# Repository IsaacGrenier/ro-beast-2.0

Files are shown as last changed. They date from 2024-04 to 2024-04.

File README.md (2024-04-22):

# Ro-Beast 2.0
Repository providing all files needed for the operation and modification of Ro-Beast 2.0, designed and built by Vardaan Malhotra, Isaac Grenier, Ben Lee, and Vince d'Entremont, also known as the Ro-Beast Battle Busters.  
  
Repository includes:
- User manual
- Altium: all schematic and PCB files for the control board
- GUI: Python files for running the GUI
- uC: all files currently programmed on the microcontroller

Software Issues to be Resolved for Full Functionality (as of 2024-04-11)
- [ ] Currently, there is a potential UART overflow issue only allowing one command to be sent to the system. For example, once positioning or a sweep is performed, the system must be turned off and back on to perform another.
- [ ] The real-time values are not being sent to the GUI. The architecture has been built out in the software, but some bugs are hindering this functionality.
- [ ] The status is not being sent to the GUI.
- [ ] The play/pause button functionality must be created.
- [ ] More warnings and errors could be created to ensure the safety and proper operation of the system.

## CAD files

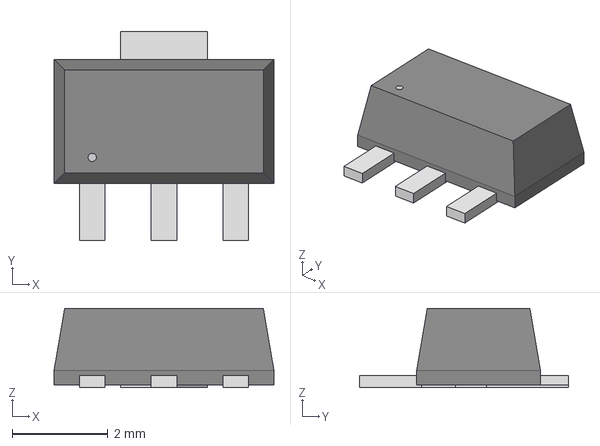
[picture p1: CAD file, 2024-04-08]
Altium/RoBeast_Control_Board/3D Bodies/SOT89_B8D_DIO.step
4.60 x 4.37 x 1.65 mm

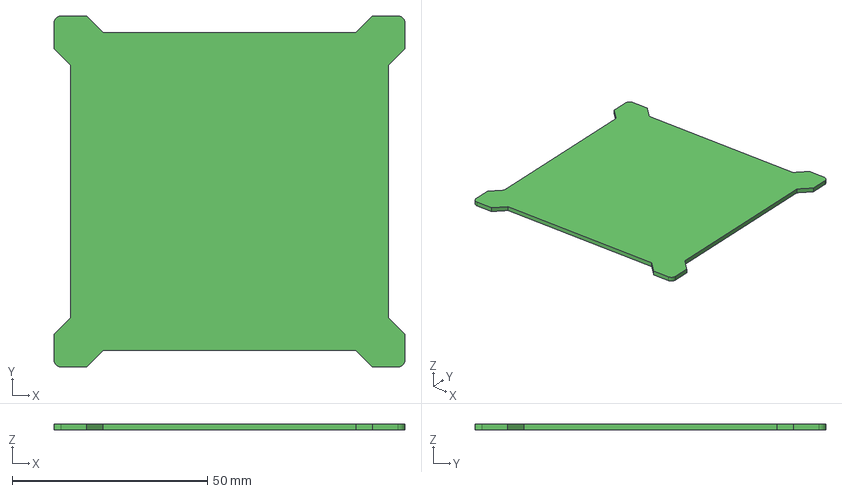
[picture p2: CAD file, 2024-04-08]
Altium/RoBeast_Control_Board/RoBeast_Control_Board_shape.step
89.9 x 89.9 x 1.58 mm

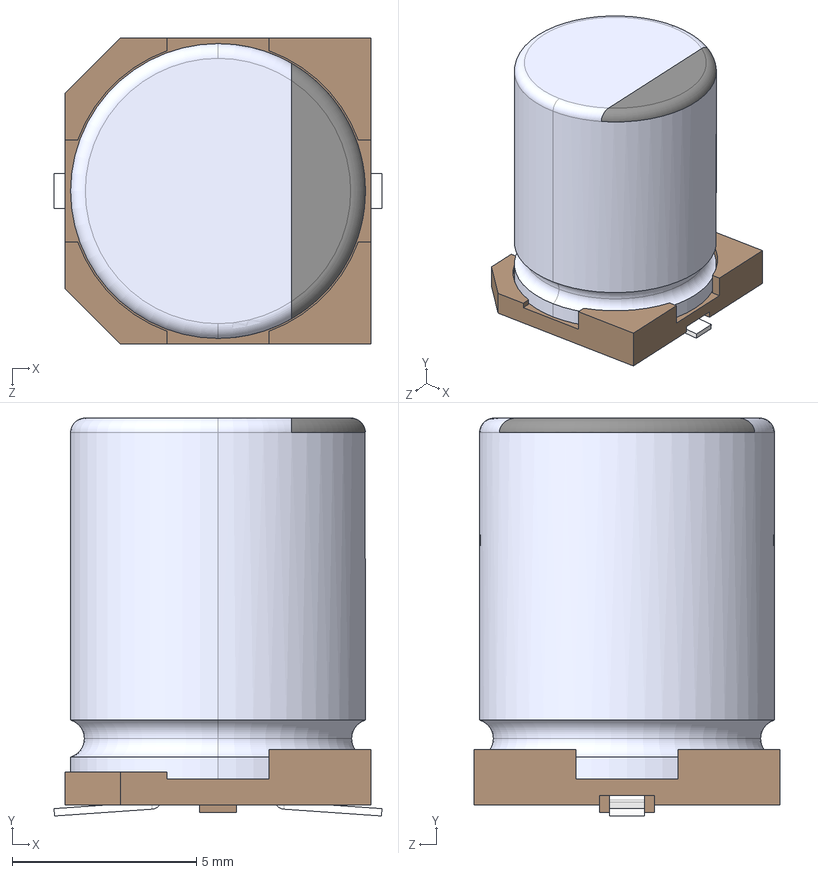
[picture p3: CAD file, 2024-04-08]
Altium/RoBeast_Control_Board/3D Bodies/UCL1V151MNL1GS.step
8.90 x 10.8 x 8.30 mm

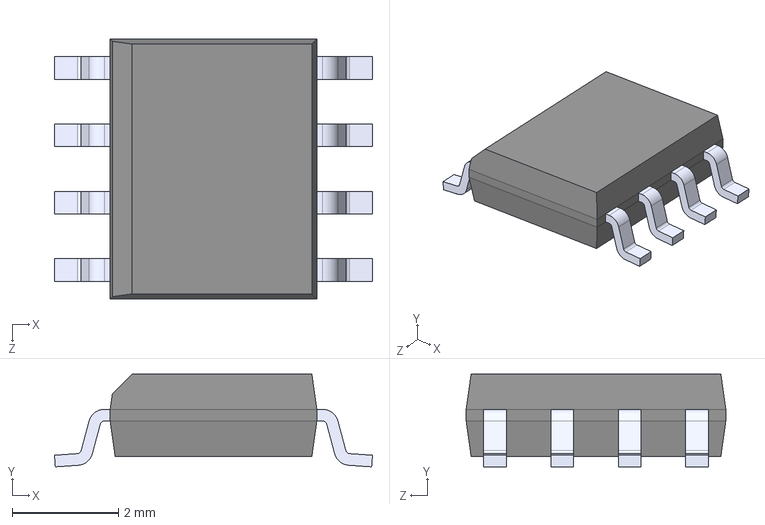
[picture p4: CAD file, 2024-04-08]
Altium/RoBeast_Control_Board/3D Bodies/DG9431EDY-T1-GE3.STEP
6.00 x 1.75 x 4.90 mm

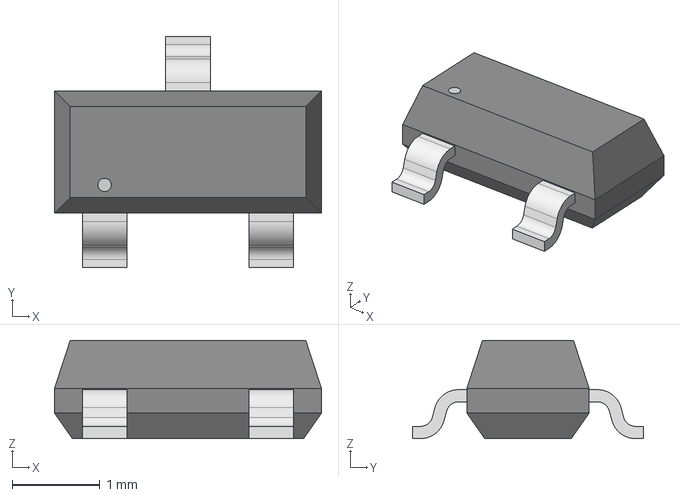
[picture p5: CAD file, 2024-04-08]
Altium/RoBeast_Control_Board/3D Bodies/SOT-23_ONS.step
3.05 x 2.64 x 1.12 mm

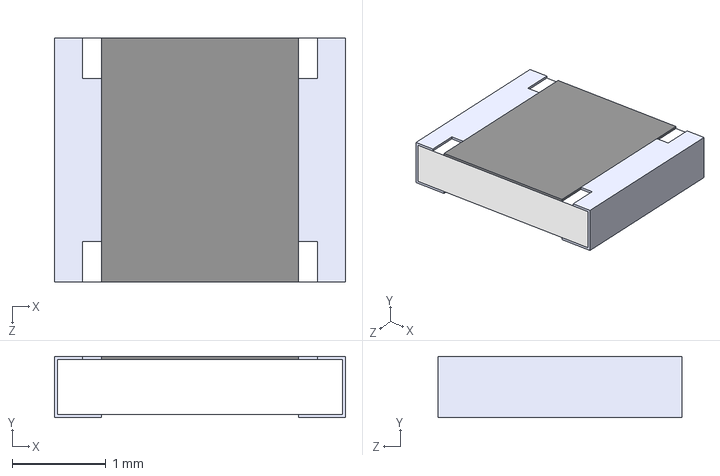
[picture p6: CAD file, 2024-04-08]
Altium/RoBeast_Control_Board/3D Bodies/RC1210JR-070RL.step
3.10 x 0.65 x 2.60 mm

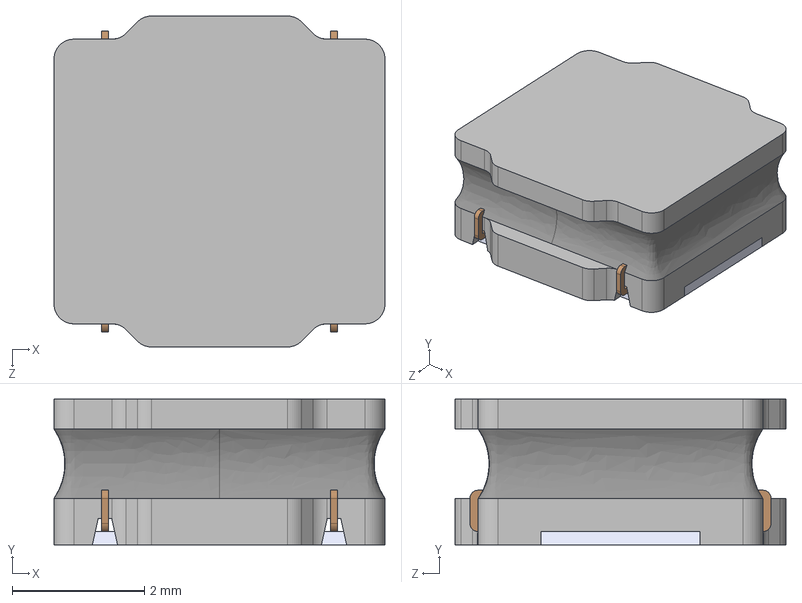
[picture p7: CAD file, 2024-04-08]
Altium/RoBeast_Control_Board/3D Bodies/LQH5BPB1R0NT0L.STEP
5.00 x 2.20 x 5.00 mm

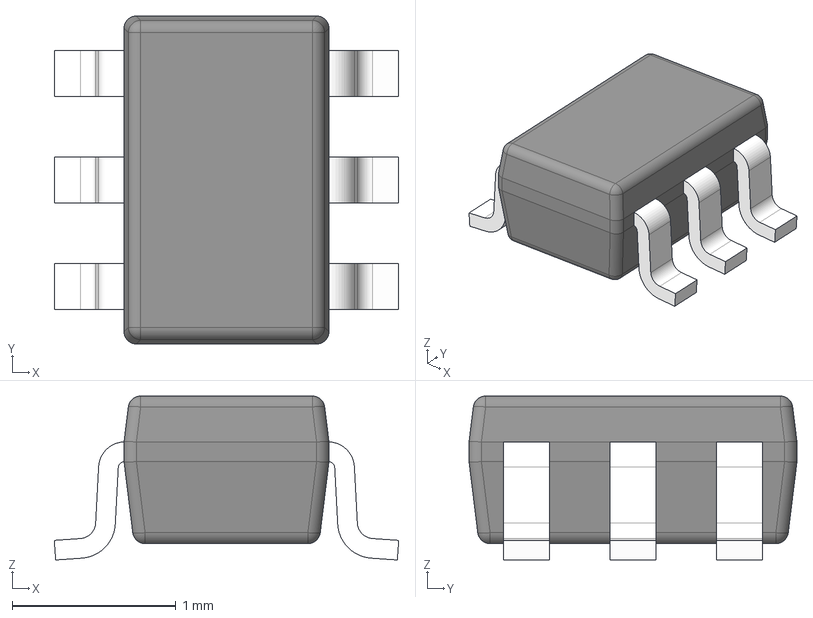
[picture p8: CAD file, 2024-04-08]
Altium/RoBeast_Control_Board/3D Bodies/DCK0006A.stp
2.10 x 2.00 x 1.00 mm
BODY-SOT
LEAD-SOT x 6
PIN1-ID

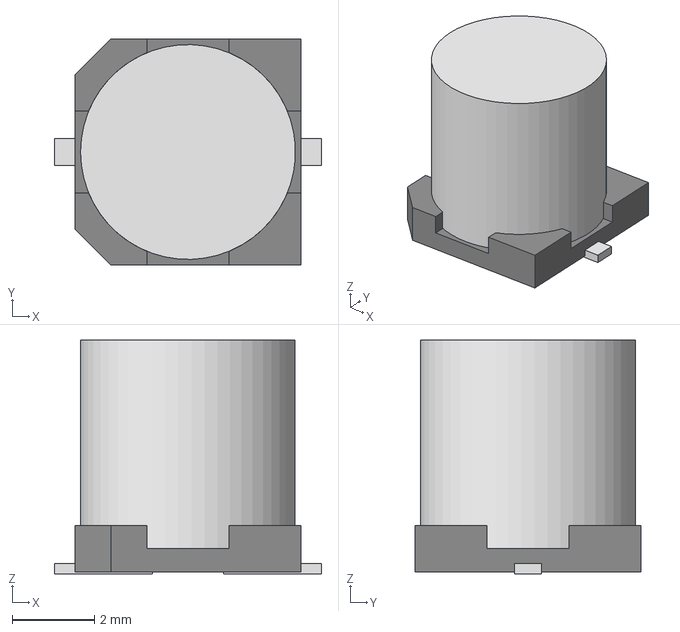
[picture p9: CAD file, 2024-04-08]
Altium/RoBeast_Control_Board/3D Bodies/EXV-9D_KEM.step
6.50 x 5.51 x 5.69 mm

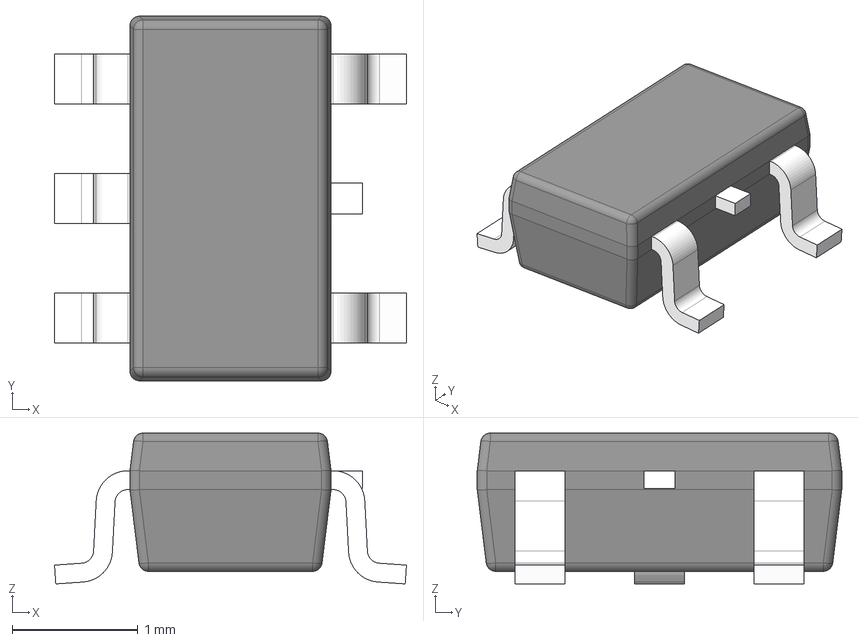
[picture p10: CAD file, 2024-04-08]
Altium/RoBeast_Control_Board/3D Bodies/DBV0005A.stp
2.80 x 2.90 x 1.20 mm
BODY-SOT
LEAD-SOT x 5
LEAD-DUMMY

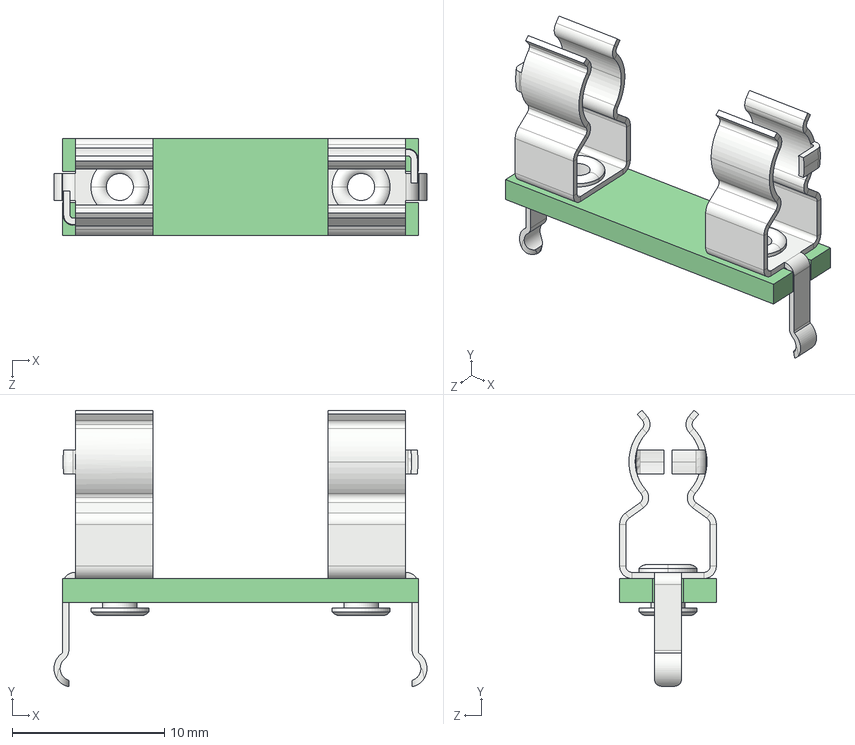
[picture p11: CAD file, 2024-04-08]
Altium/RoBeast_Control_Board/3D Bodies/3527.step
24.5 x 18.2 x 6.35 mm

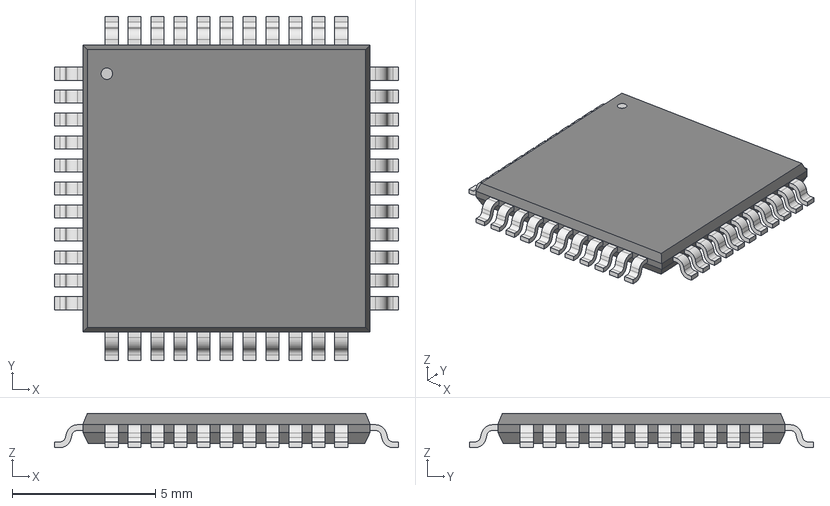
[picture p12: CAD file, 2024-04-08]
Altium/RoBeast_Control_Board/3D Bodies/TQFP44_10x10MC_MCH.step
12.0 x 12.0 x 1.20 mm

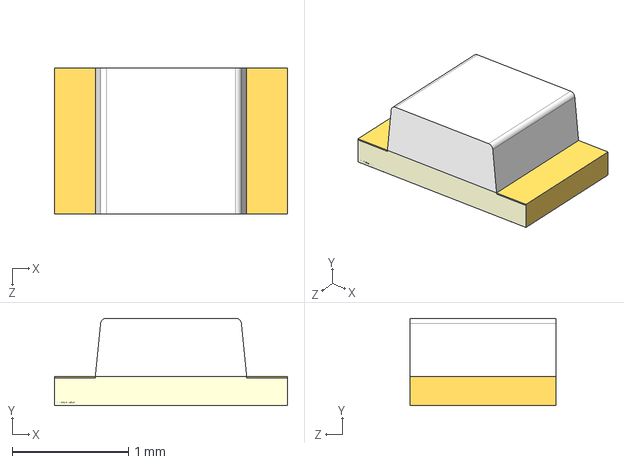
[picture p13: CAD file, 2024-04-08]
Altium/RoBeast_Control_Board/3D Bodies/APT2012.STEP
2.00 x 0.75 x 1.25 mm

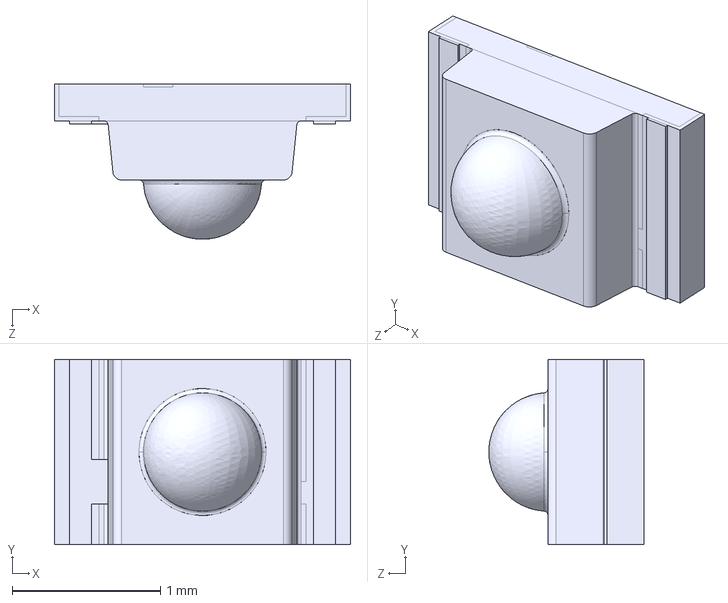
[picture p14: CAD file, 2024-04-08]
Altium/RoBeast_Control_Board/3D Bodies/APTD2012.IGS
2.00 x 1.25 x 1.05 mm

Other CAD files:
Altium/RoBeast_Control_Board/3D Bodies/DCK0005A.stp
Altium/RoBeast_Control_Board/3D Bodies/PH1RA-03-UA.STEP
Altium/RoBeast_Control_Board/3D Bodies/54-00128.STEP
Altium/RoBeast_Control_Board/3D Bodies/IPD50P04P4L-11--3DModel-STEP-56544.STEP
Altium/RoBeast_Control_Board/3D Bodies/015246043.stp
Altium/RoBeast_Control_Board/3D Bodies/0217005.MXP.STEP
Altium/RoBeast_Control_Board/3D Bodies/026013114.stp
Altium/RoBeast_Control_Board/3D Bodies/039291188.stp
Altium/RoBeast_Control_Board/3D Bodies/0731375003--3DModel-STEP-56544.STEP
Altium/RoBeast_Control_Board/3D Bodies/0805.step
Altium/RoBeast_Control_Board/3D Bodies/1206.step
Altium/RoBeast_Control_Board/3D Bodies/473461001.stp
Altium/RoBeast_Control_Board/3D Bodies/530470510.stp
Altium/RoBeast_Control_Board/3D Bodies/530480210.step
Altium/RoBeast_Control_Board/3D Bodies/530480410.step
Altium/RoBeast_Control_Board/3D Bodies/530480510.step
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

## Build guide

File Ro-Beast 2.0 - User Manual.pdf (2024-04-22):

# Ro-Beast 2.0: User Manual

This is the ultimate user manual for the anechoic chamber testing platform, the Ro-Beast 2.0,

designed by Group 11 in the Mechanical Engineering Section of the 2023-24 ENGG 4000 Senior

Design Project cohort. See the following QR code for the full CAD model and more.

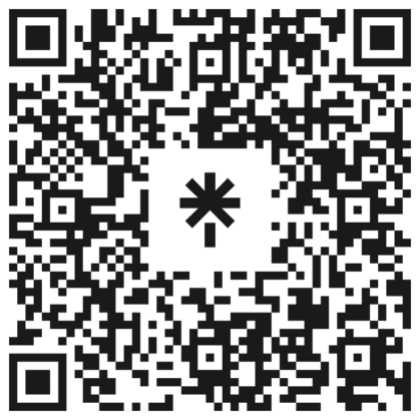
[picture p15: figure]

Figure 1. QR code to Full CAD assembly, Animations, and PCB Schematics

Ben Lee

Isaac Grenier

Vardaan Malhotra

Vincent d’Entremont

11 April 2024

## Contents

## Key Terms

EUT: Equipment under Test

Ro-Beast 2.0: the physical structure, hardware, and code of the testing platform

GUI: Graphical User Interface

## Operating Limits:

Vertical Elevation:

- Range – 1.04 m to 1.93 m
- Speed – 0 to 10 mm/s
- Measurement interval – 0.1 mm to (range – current height)
- Resolution – 6 microns/step

Tilt Range:

- Range – 0° to 90°
- Resolution – 15°

Azimuthal Rotation:

- Range – 0° to 360°
- Speed – 2°/s to 30°/s
- Measurement interval – 0 to 99.9˚ (less than (range – current azimuth) to successfully

measure)

- Angular step resolution - 0.0321°/step

## Safety Concerns

First and foremost, there are some safety concerns with the use and operation of this device, so it is up to the User to operate at their own risk, or for future senior design groups to improve upon. In the meantime, no persons should be within 2m of the Ro-Beast 2.0 while operating the elevation mechanism.

### 1. Pinch Points

a. There are a few main pinch points that could crush a finger. Firstly, the gap between the top plate and the support plate gets very small when at the lowest position. Therefore, wire mesh finger guards should be installed in place. In the meantime, no persons shall be within 2m of the Ro-Beast 2.0 when the elevation is operating.
b. Spur gears. There is an open set of spur gears which drives at fairly high RPM at the max speed and someone could get their hair caught inside or fingers.
c. Bevel Gears. While the bevel gearset that drives the rotation mechanism is hidden from view, nothing stops the user from reaching underneath the swing bracket and touching the bevel gears when operating a rotation sweep. This is dangerous and should not be done.

### 2. Lack of Load Testing:

a. The Ro-Beast 2.0 was finished late in the semester and therefore, full testing was not able to be carried out. While the team determined that the full applied loads of 10 kg EUT and 10 kg counterweight could be driven under the desired speeds, there WAS NOT a way to test the full load when tilted. Therefore, the user should not attempt to place EUTs greater than 1kg on the Ro-Beast 2.0 while tilted, unless they are doing so in a safe manner to determine the limits of the Ro-Beast 2.0.

### 3. Dropped Objects

a. Since this device is quite tall at the maximum range, nobody should place foreign objects on the top plate or the EUT mount for the risk of them falling off and damaging other equipment.

## Construction and Assembly Plan

The construction of the Ro-Beast 2.0 involves many parts both electrically and mechanically.

Any fabrication procedures such as welding, cutting, drilling, bending, grinding, sanding, and

tapping were performed by the team in the UNB machine shop. More complicated parts that

require precise fits with the lathe or CNC were fabricated by machinist Tony Guimond.

The lower supporting structure is comprised of all the parts shown in the exploded view of

Figure 2, and the procedure is as follows. The 1m long support legs could be placed within the

holes in the steel support feet. Use wooden spacers to keep the support feet parallel and at the

desired spacing. Place the support plate on top of the support tubes. The support plate is bolted

loosely to both the support tube flanges, after which the cross bracing would be placed and bolted down. M10 bolts and nuts were used to fasten all structural components to the support plate and

M8 bolts, nuts and washers were used to fasten the cross bracing to the support feet.

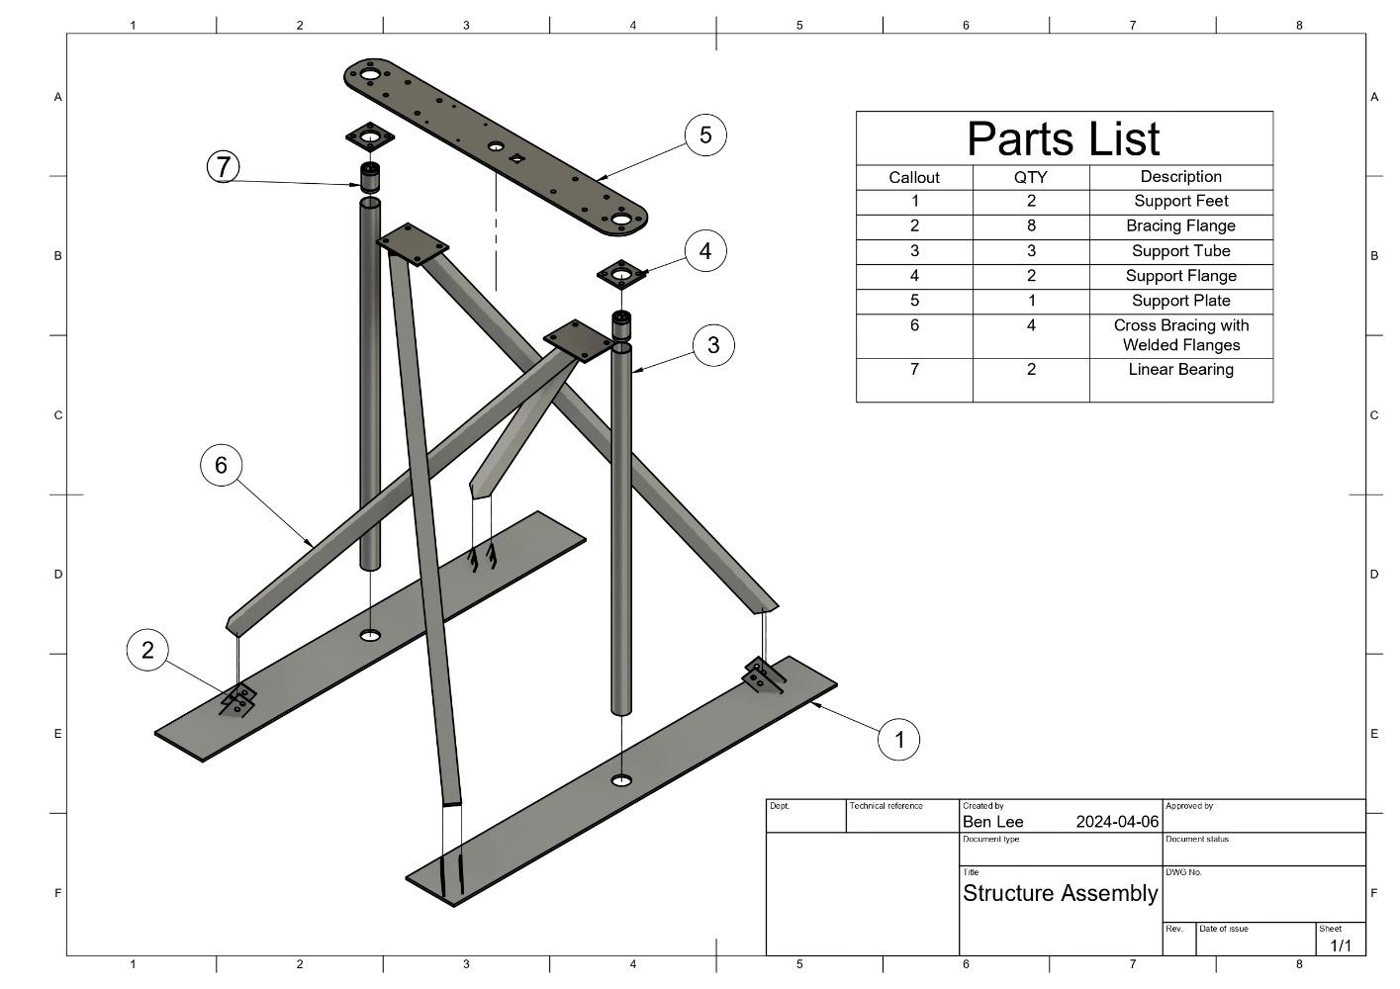
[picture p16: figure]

Figure 2. Bottom Structure Assembly Exploded View

After the lower structure was assembled the upper structure was fabricated and assembled as

shown in Figure 3. The oil-impregnated flanged sleeve bearings were press-fit into the sides of the

swing bracket, the tilt shaft had M10 threads tapped into the end, slid through the flange bearings,

and the whole swing bracket was bolted to the tilt brackets with custom oversized washers. This

ensured that the tilt shaft was pulled into the holes in the tilt bracket which would take the load so

the bolt would not be in shear. The tilt brackets and counterweight slider were bolted to the top

plate using ¾” UNC aluminum bolts and nuts. The linear rails were fastened to the top plate with

standard M10 nuts and washers. The ball screw was bolted on with an M12-1 fine thread locknut

after first putting a steel spacer beneath the top plate.

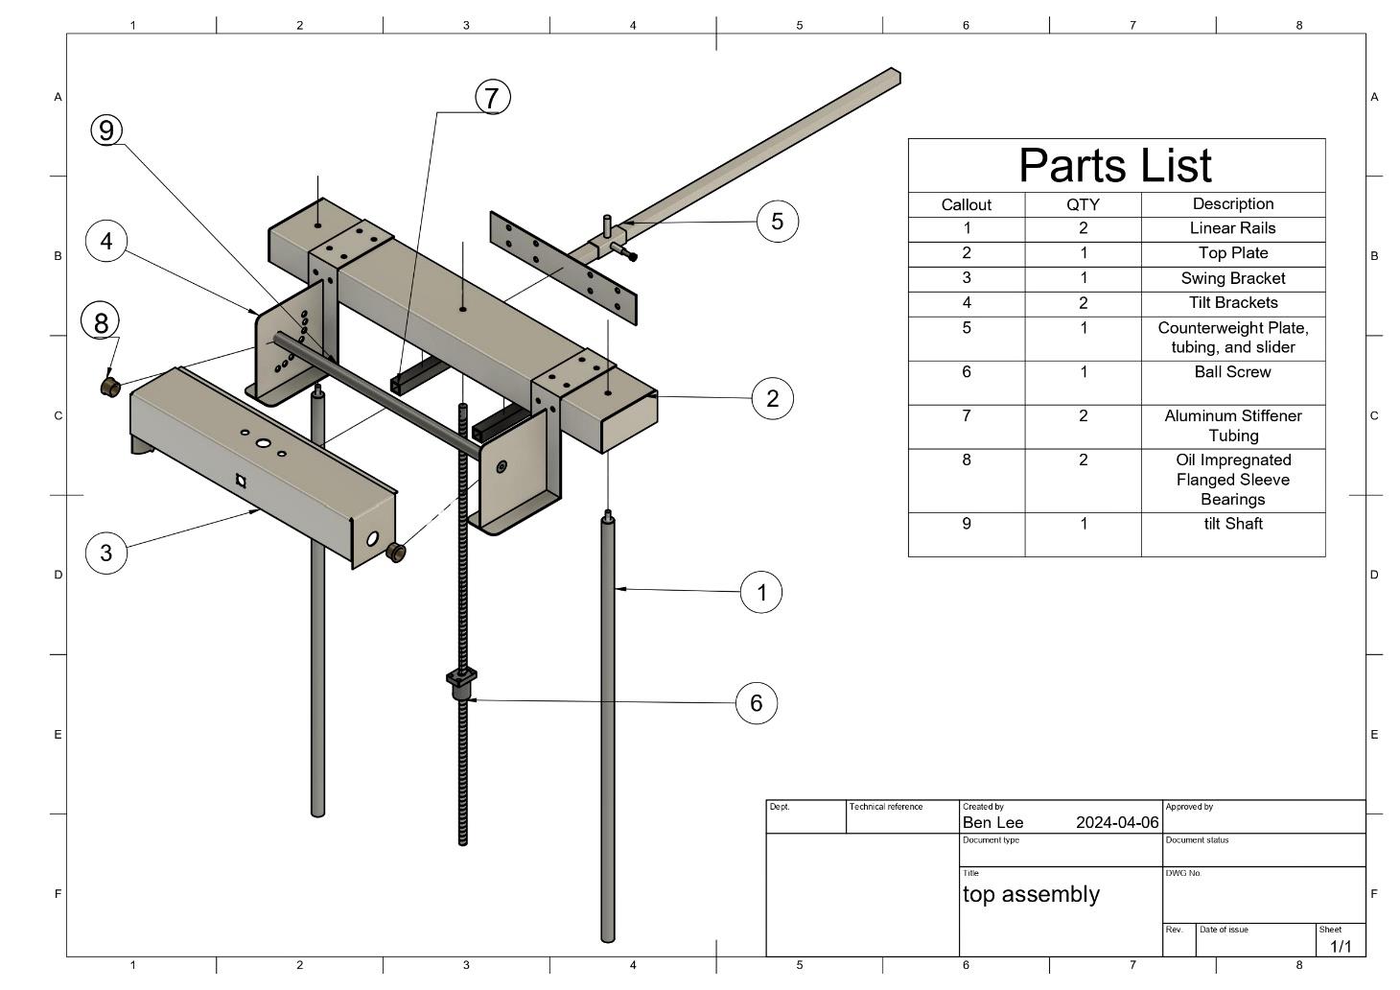
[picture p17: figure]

Figure 3. Top Structure Assembly Exploded View

An exploded view of the rotation mechanism assembly is shown in Figure 4. The EUT mount

was cut on a bandsaw and sanded from a 1” thick 9” diameter plate from plywood. The EUT shaft

adapter was machined to spec from a 3” piece of aluminum on the lathe and CNC, then screwed

into the mount with wood screws. The EUT shaft was fixed into the mount and adapter with set

screws. An oil-impregnated thrust washer was placed over the hole in the swing bracket and the

shaft was slid in. Underneath, the flange bearing was bolted to the swing bracket and the bevel

gear was fixed to the EUT shaft’s exposed end with set screws. Then the motor was bolted onto

the swing bracket’s front face and secured with M2.5 screws. The pinion was attached to the shaft

with a set screw and the encoder was mounted to the back of the motor. Assembling the rotation

assembly was easily done when not attached to the tilt brackets and top plate, as the tilt shaft had

to be removed to access the bolts for the motor.

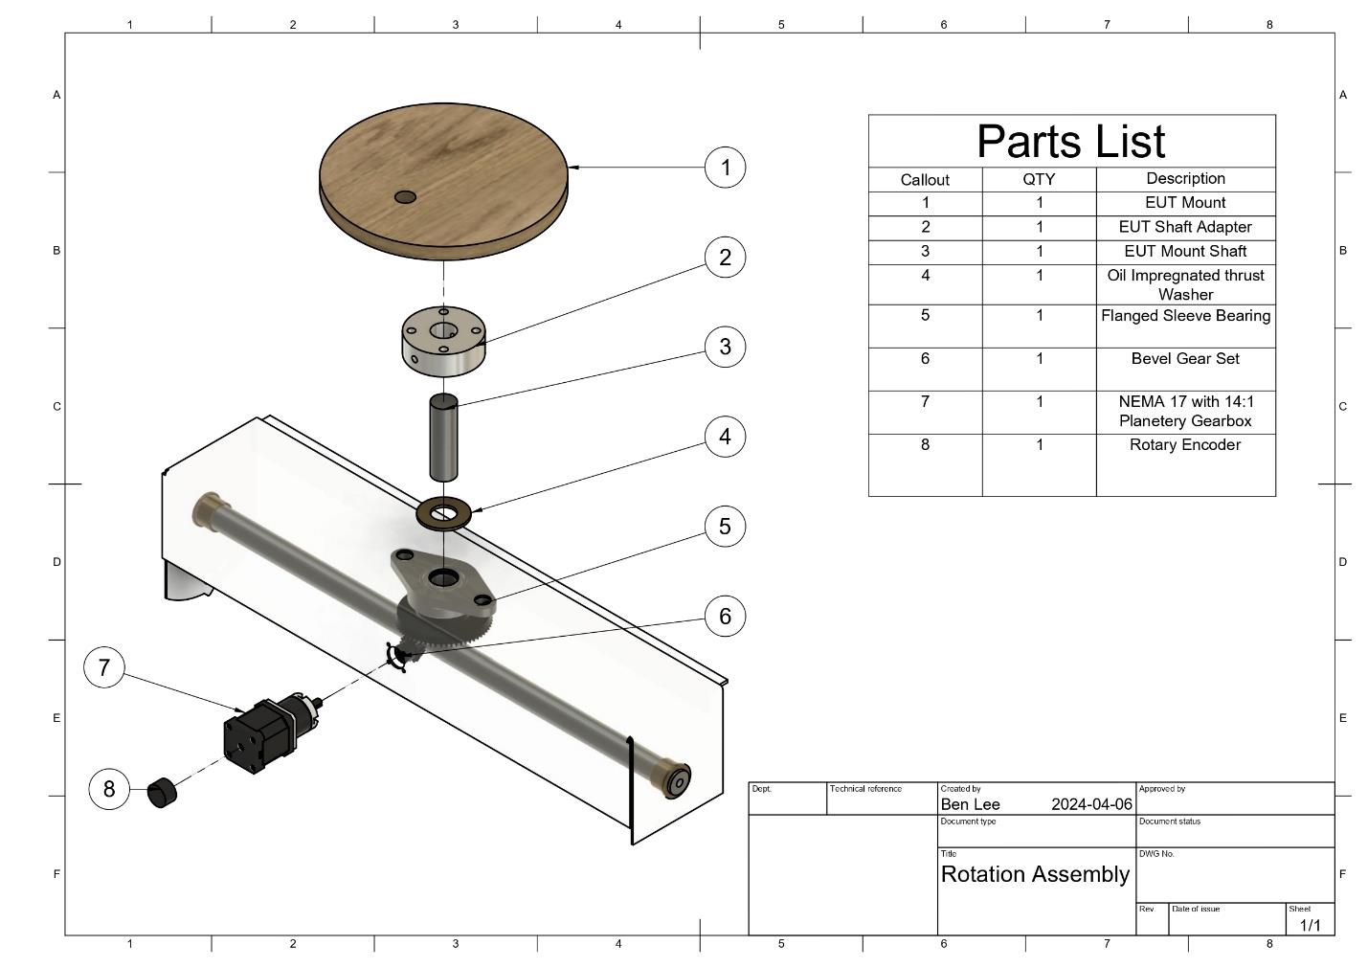
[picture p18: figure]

Figure 4. Rotation Assembly Exploded View

The assembly figure for how the elevation motor and ball screw are assembled is shown in

Figure 5. The motor was bolted to the support plate after having a shaft keyway cut into both itself

and the corresponding spur pinion. The set screw locks the pinion in place. Ensure the spur gear is

bolted to the ball nut tightly. The spacer was placed over the hole in the support plate, a needle

roller thrust bearing was placed on top, the spur gear was bolted on the ball screw nut, and the ball

screw and nut were slid into the hole in the support plate. A 2-piece 3D printed housing was

designed to hold the DC electromagnetic brake onto the back of the stepper motor since the bolt-

hole pattern did not align. Before the motor is bolted on, its motor-brake 3D printed housing piece

is slid over, then the DC electromagnetic brake is slid into its housing piece, and the two parts

were bolted together with standard M4 screws.

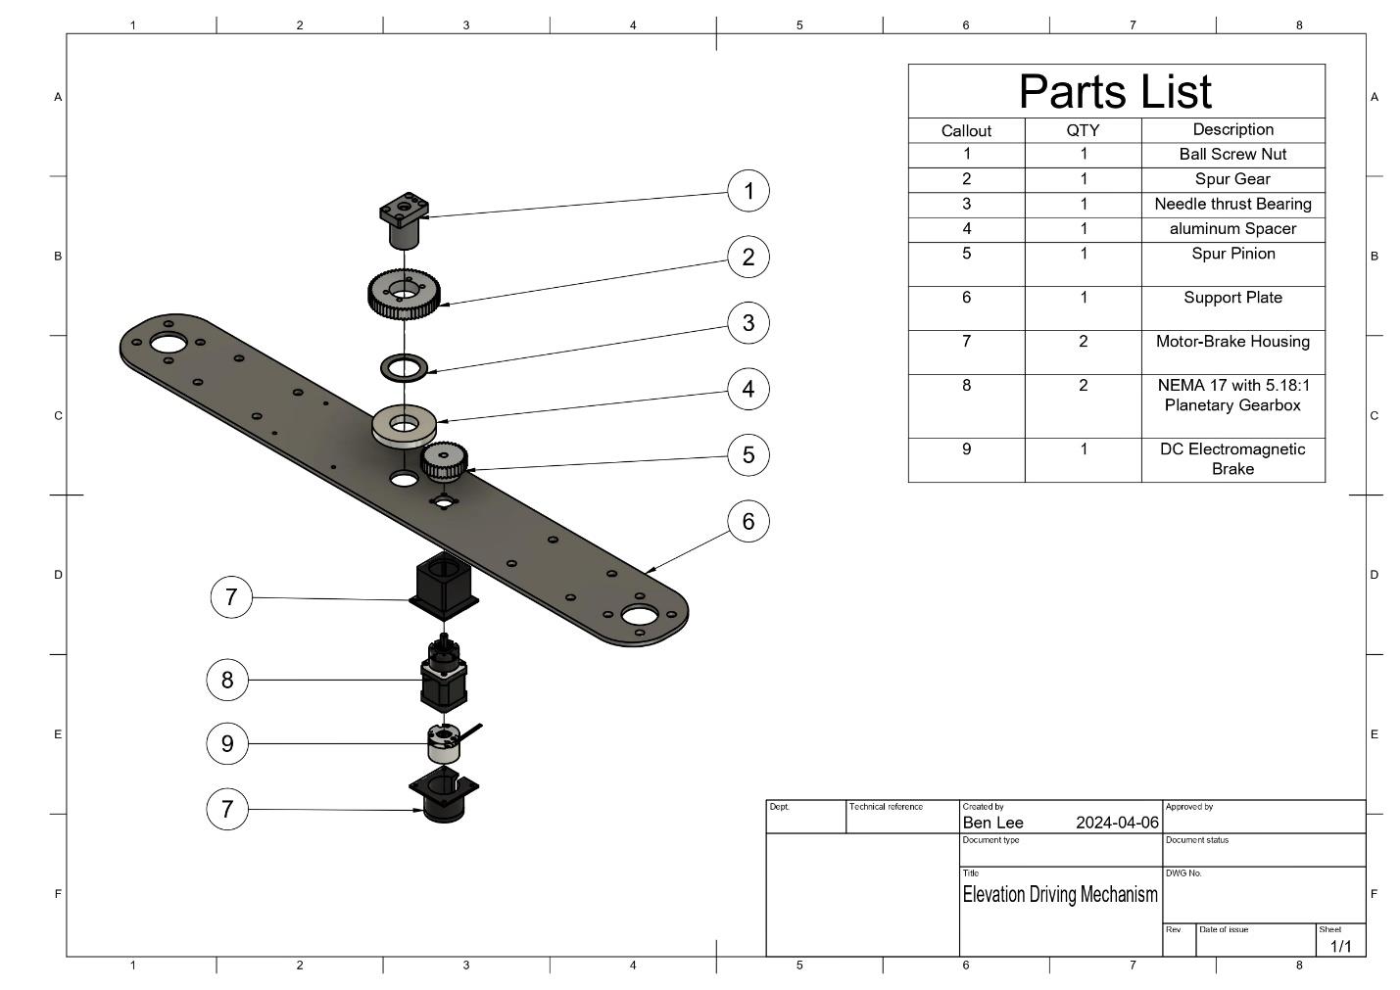
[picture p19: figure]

Figure 5. Elevation Driving Mechanism Assembly Exploded View

Once the structure has been completely assembled, the team placed the limit switches on the

tilting, rotation, and vertical translation mechanisms with M2 screws as well as 3D-printed switch

mounts. The PCB was bolted to the bottom of the support plate and wires were routed with enough

slack for the full range. The 3D printed limit switch trigger must be screwed onto the bottom of

the ball screw which triggers the elevation limit switch defining the maximum height position.

Once the aforementioned tasks and sub-assemblies were completed, the total assembly would be

put together by first placing the ball screw and linear rails in the lower support structure. Then the

top structure could be lowered down onto the linear rails and bolted in place, as shown in Figure

6.

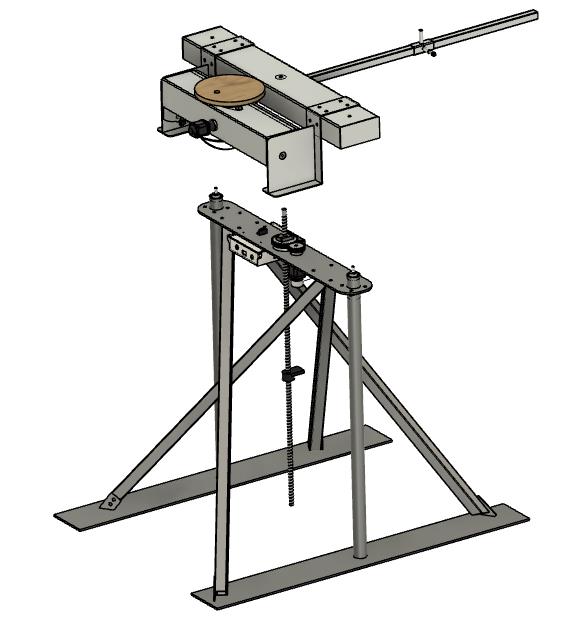
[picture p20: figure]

Figure 6. Full Assembly Placement View

## Apparatus

Ro-Beast 2.0

The Ro-Beast 2.0 has many components, so this section will serve to familiarize the user with those features. See the figure below for a high-level view of the parts of the Ro-Beast 2.0, followed by additional views for the three main mechanisms. Refer to the

Construction and Assembly Plan exploded views for the names of each part.

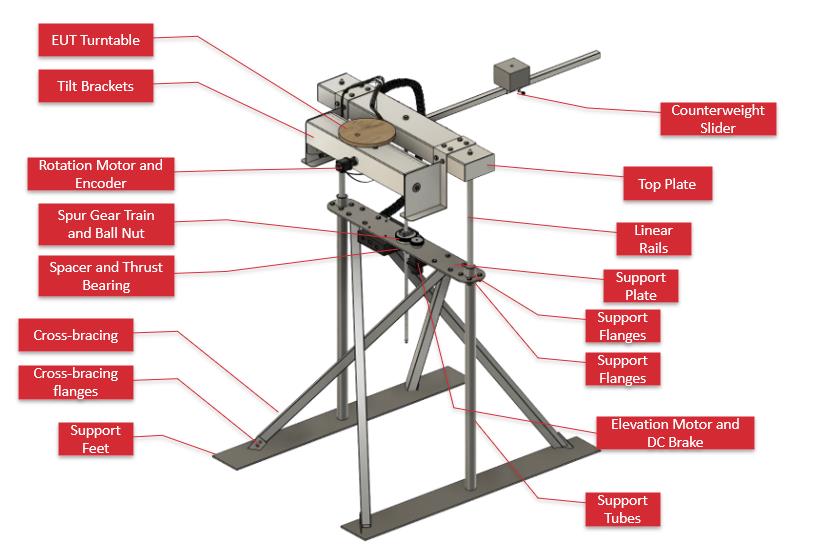
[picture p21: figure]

Figure 7. High-Level Diagram of the Ro-Beast 2.0

The following figures are the exploded views of the sub-assemblies: rotation assembly, elevation

assembly, and the tilt mechanism. Figure 8 serves to familiarize the user with the operating

mechanism for the azimuthal rotation sweep. It is driven by a NEMA 17 stepper motor with a

14:1 gearbox which drives bevel gears to rotate the EUT mount at the desired speed and

positions. There is a rear-mounted encoder for positional feedback, as well as a limit switch that

triggers for home position.

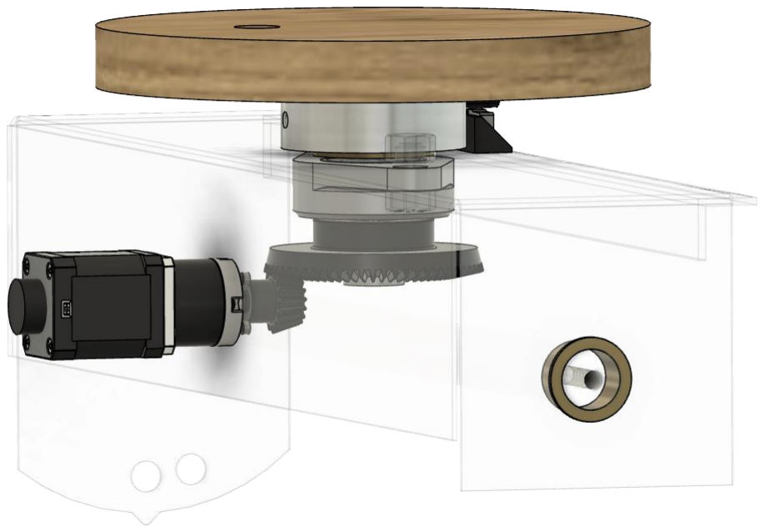
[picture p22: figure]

Figure 8. Rotation Mechanism

Figure 9 shows how the elevation driving mechanism is assembled. Essentially there is a

NEMA17 stepper motor with a 5.18:1 gearbox that drives spur gears to rotate the nut of the ball

screw which lifts the ball screw up and down. There is a DC electromagnetic Brake on the back

of the NEMA17 motor to provide a locking torque when the motors are turned off. Two linear

rails slide up and down in support shafts with linear bearings press fit into the support shafts to

counteract moments. A limit switch on the top of the support plate and one on the bottom trigger

the end range positions.

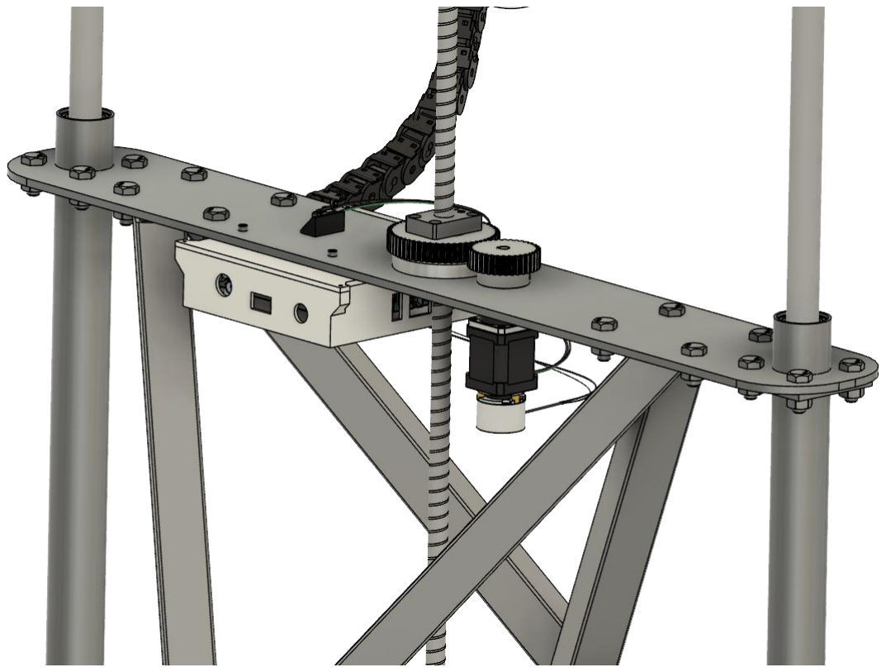
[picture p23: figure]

Figure 9. Elevation Mechanism

Figure 10 shows the inside of the tilt mechanism. A manual pin design is used here to offer the

user 15 degrees per increment between 0° and 90°. Limit switches will trigger at each of the

positions for real-time feedback. Ensure both pins are in fully by looking from the view shown

below.

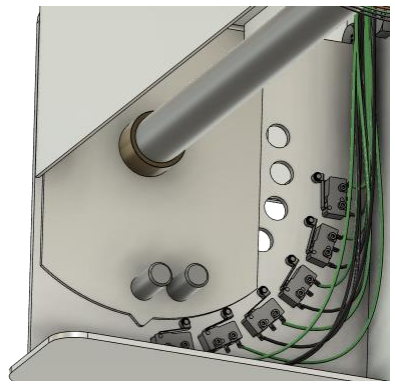
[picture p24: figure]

Figure 10. Tilt Mechanism

## System Checklist

This section will provide a list of key items to ensure are connected and in the proper position

before attempting to perform any sweep functionality, assuming the Ro-Beast 2.0 has already

been constructed and assembled as per the construction section.

- Ensure all limit switches are in the correct position and align with the corresponding

triggers.

- Ensure the wires from the PCB box will not get caught on any moving parts
- Ensure all peripherals are securely plugged into the PCB
- Ensure both sets of gears are meshing
- Ensure the ball screw lock nut is tight (the screw should not be able to rotate)

## Quick Start Guide

How to Mount an EUT to the Ro-Beast

Currently, the team has not designed a versatile mounting method to accommodate a wide range

of EUTs as it was not a focus of the scope. Currently, the EUT can just be screwed into the

wooden mount.

How to Start the Ro-Beast 2.0

Requirements:

1. Constructed Ro-Beast 2.0
2. Actuators and sensors are plugged into the control board
3. USB cable connecting the host computer to the control board
4. BNC cable connecting the VNA to the control board
5. Required Python files are on the host computer

Use the DC barrel plug to power the control board. Run the Python file “Ro-Beast.py” to start

the GUI. Upon startup, Ro-Beast 2.0 will home itself to 1.04 m and 0˚, indicated with limit

switches.

How to Position the Ro-Beast
As outlined in Figure 11 below, two parameters must be set to position Ro-Beast 2.0: the desired

height and the desired azimuth.

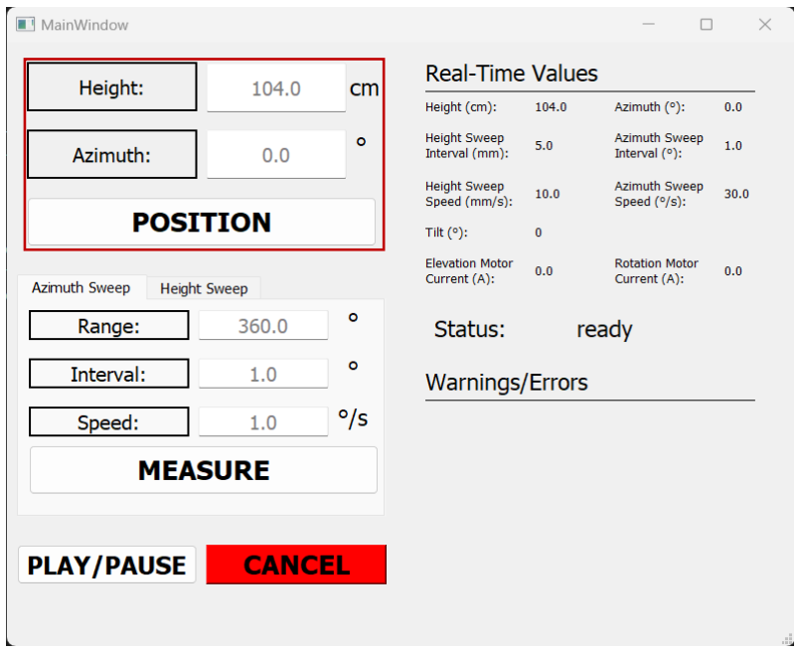
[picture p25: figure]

Figure 11: GUI showing the positioning section

If the height and azimuth in the text boxes differ from what is desired, enter the desired values,

ensuring they are within the restrictions outlined in the Operating Limits: section. Once the

values are correctly configured, press the “POSITION” button and wait for Ro-Beast 2.0 to

finish moving and return to standby.

How to Take an Azimuth Sweep

As outlined in Figure 12 below, three parameters must be set to position Ro-Beast 2.0: the

desired final azimuth (range), the desired interval between measurement pulses (interval), and

the desired sweep speed (speed).

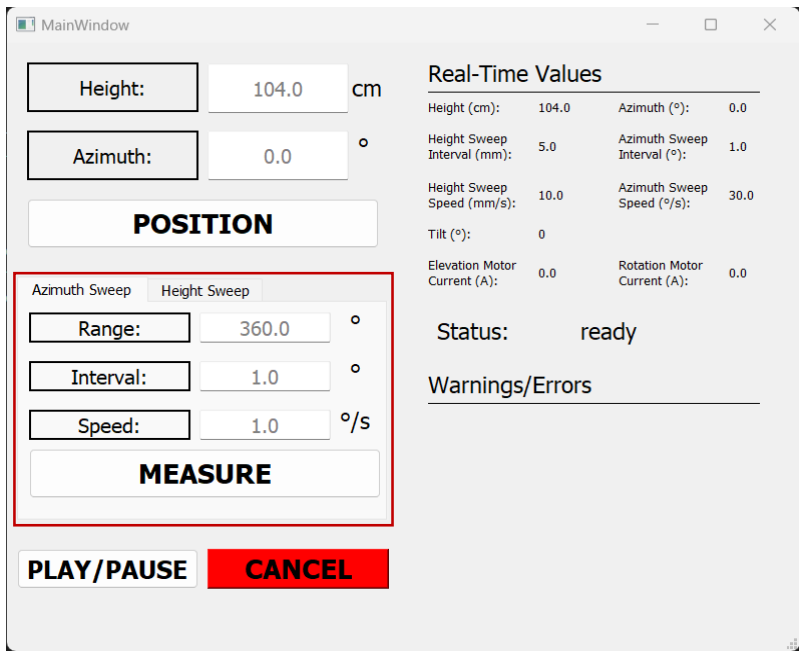
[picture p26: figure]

Figure 12: GUI showing Azimuth Sweep tab

If the range, interval, and speed text boxes differ from what is desired, enter the desired values,

ensuring they are within the restrictions outlined in the Operating Limits: section. Note that the

measurement interval must be less than the azimuthal distance the Ro-Beast 2.0 will be

travelling. Once the values are correctly configured, press the “SWEEP” button. Once the sweep

is completed, Ro-Beast 2.0 will re-home itself to 1.04 m and 0˚ and will then return to standby.

How to Take a Height Sweep

As outlined in Figure 13 below, three parameters must be set to position Ro-Beast 2.0: the

desired final height (range), the desired interval between measurement pulses (interval), and the

desired sweep speed (speed).

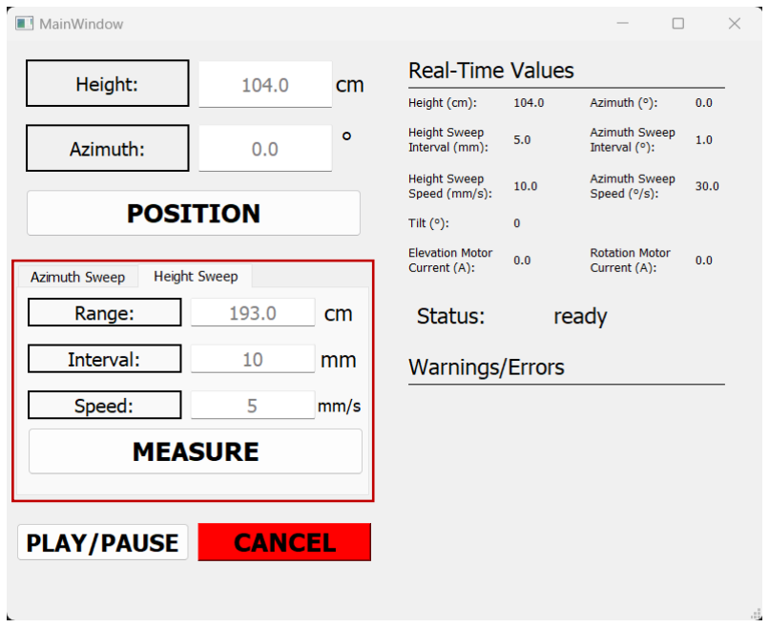
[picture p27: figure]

Figure 13: GUI showing Height Sweep tab

If the range, interval, and speed text boxes differ from what is desired, enter the desired values,

ensuring they are within the restrictions outlined in the Operating Limits: section. Note that the

measurement interval must be less than the distance Ro-Beast 2.0 will be travelling. Once the

values are correctly configured, press the “SWEEP” button. Once the sweep is completed, Ro-

Beast 2.0 will re-home itself to 1.04 m and 0˚ and will then return to standby.

How to Adjust Tilt

1. Hold the swing bracket
2. Remove pins from the tilt bracket
3. Rotate the swing bracket to the desired angles. Ensure the holes on the tilt bracket are

aligned with the holes on the swing bracket

4. Insert pins to lock the swing bracket

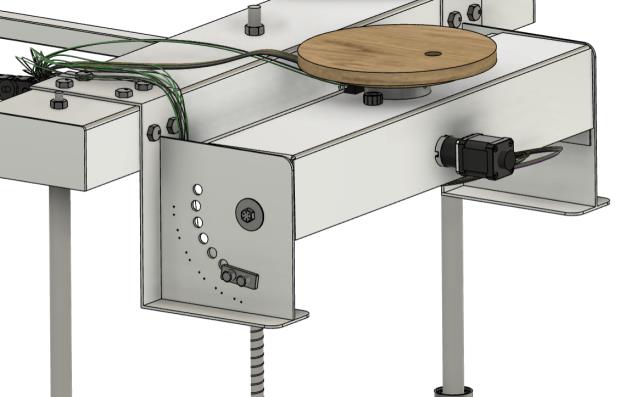
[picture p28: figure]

How to Adjust the Counterweight

See the attached Excel worksheet for how to adjust the counterweight to prevent deflection and

promote levelness. As shown in Figure 14, the user must input four variables to determine the

position of the counterweight along the slider.

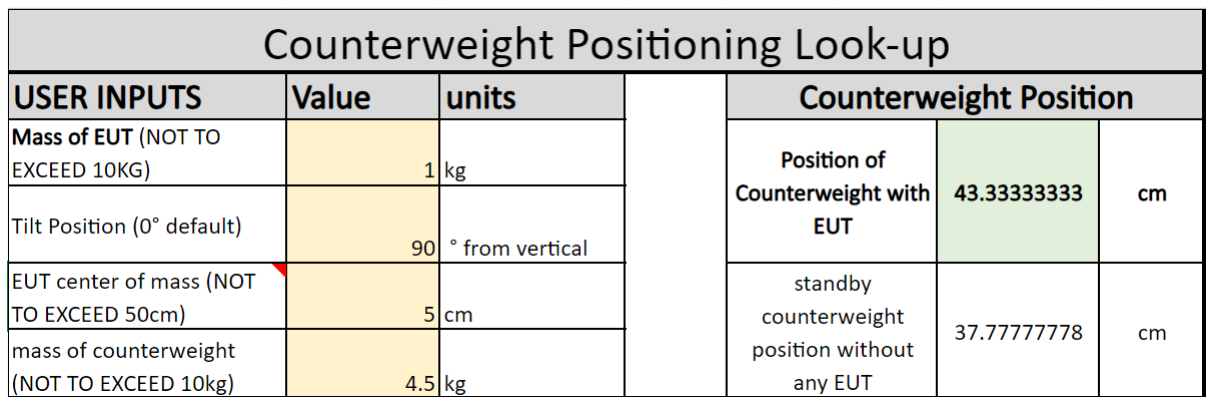
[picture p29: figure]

Figure 14. Counterweight Positioning Look-up

Variables:

1. Mass of EUT – this is the mass in kg and cannot exceed 10 kg
2. Tilt Position – this is the angular tilt position shown by the GUI in degrees

3. EUT Center of Mass – this is how far out the center of mass of the EUT is from the

face of the EUT mount Figure 15. This parameter can be determined by placing the EUT

on a slim rod and positioning it until it balances, like a see-saw.

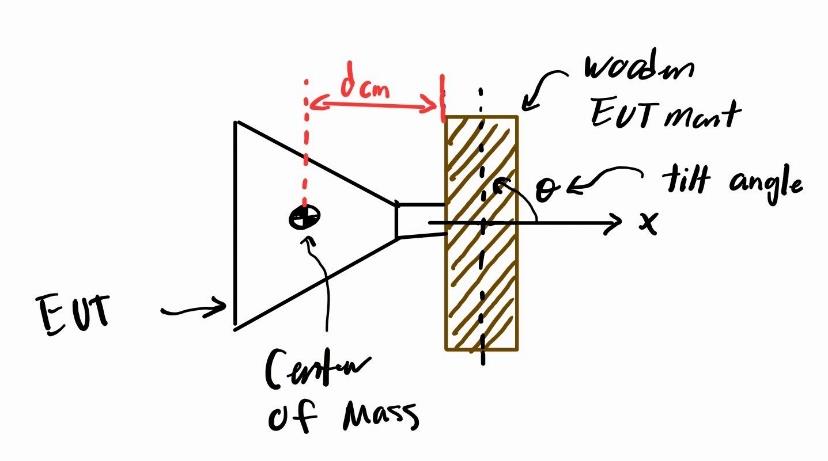
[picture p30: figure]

Figure 15. Visual Diagram of Center of Mass

4. Mass of Counterweight – the mass of the counterweight must not exceed 10kg. The

counterweight should have a central hole to slide onto the counterweight slider which

will prevent it from falling. Any small gym weight plate should work. Use the tightening

bolt to lock the slider in place.

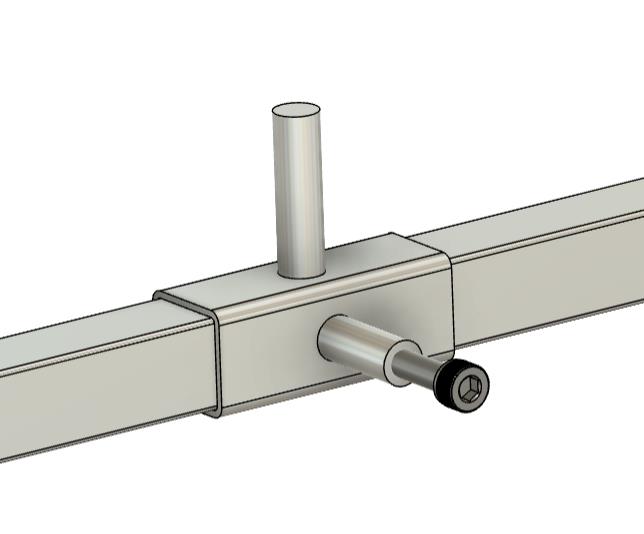
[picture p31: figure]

Figure 16. Counterweight Slider

Once all those values are entered, the box in green will tell you how far to position the slider

along the rod, measured FROM the surface where the slider is bolted to the top plate. If the

position that shows up is farther than 90 cm, something is wrong. Either the counterweight is too

light, the EUT exceeds 10 kg, the position of the center of mass exceeds 50 cm, or a combination

of these things. The slider cannot be positioned farther than this. Use a ruler to get it to an

approximate location.

Other GUI functions
Play/pause: when this button is pressed, the system will pause in its current state and maintain all

current values. Once this button is pressed again, the system will resume what it was doing.

Cancel: when this button is pressed, the system will re-home itself to 1.04 m and 0˚ and await in

standby.

How to Shut off the Ro-Beast 2.0

Remove power from Ro-Beast 2.0, close the GUI, and disconnect the power cable, USB cable,

and VNA cable.

## Software Issues to be Resolved for Full Functionality (as of 2024-04-11)

- Currently, there is a potential UART overflow issue only allowing one command to be

sent to the system. For example, once positioning or a sweep is performed, the system

must be turned off and back on to perform another.

- The real-time values are not being sent to the GUI. The architecture has been built out in

the software, but some bugs are hindering this functionality.

- The status is not being sent to the GUI.
- The play/pause button functionality must be created.
- More warnings and errors could be created to ensure the safety and proper operation of

the system.

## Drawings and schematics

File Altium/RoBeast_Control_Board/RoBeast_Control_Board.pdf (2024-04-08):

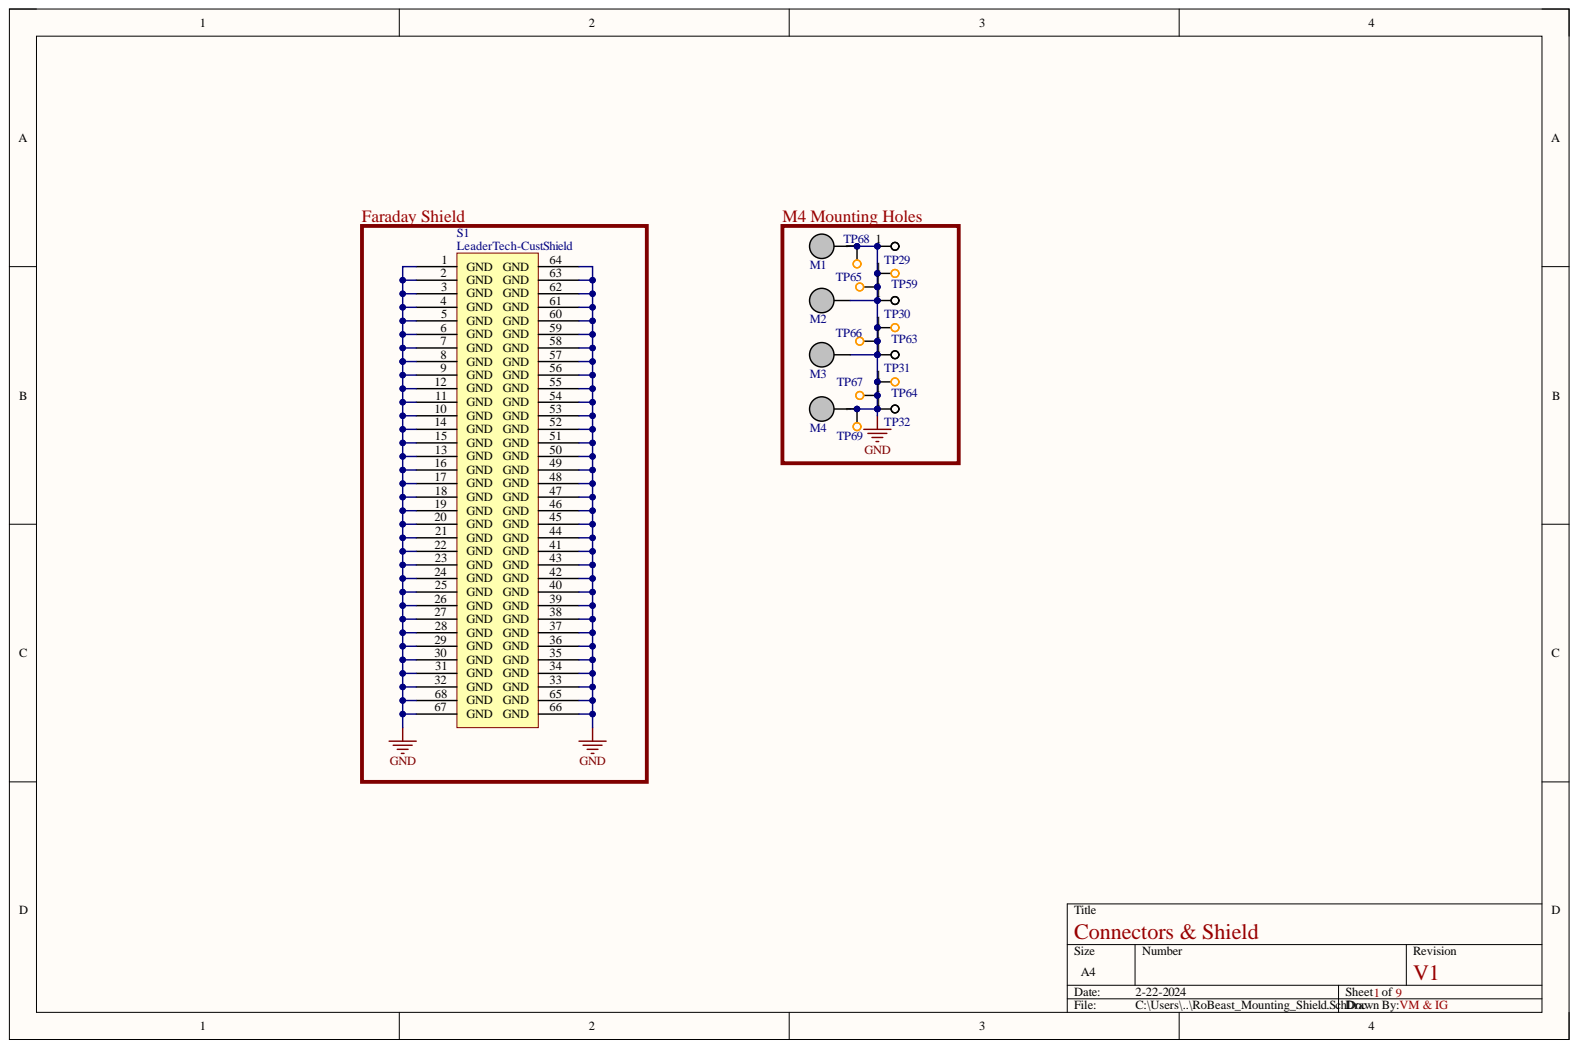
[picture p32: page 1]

Siz e A4 | Numb e r | R evisio n V1

Da te : 2-22-2 0 24 | She et of 1 9
File : C:\Use rs\. .\RoB e ast_Mounting_Shie l d . S | c hDr Doacwn By: VM & I G

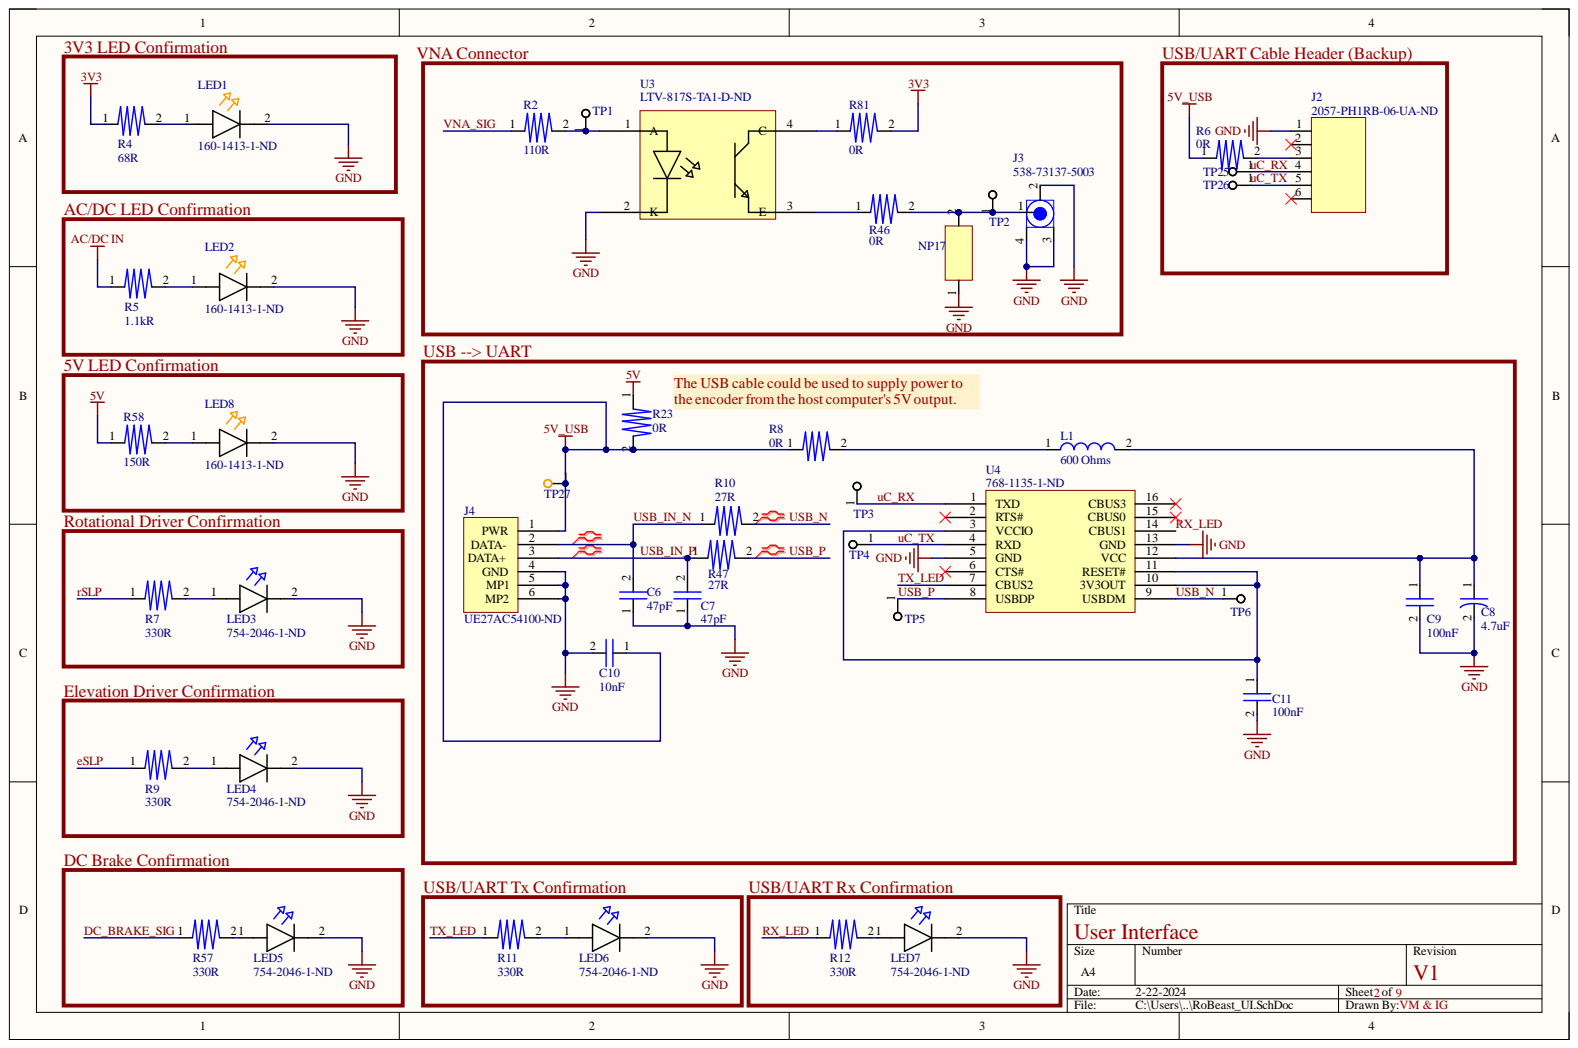
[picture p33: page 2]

USB/UART Cable Header (Backup)

AC/DC LED Confirmation

the encoderfrom the host computer's 5Voutput.

Size A4 | Number | Revision

Date: 2-22-2024 | Sheet of
File: C:\Users\..\RoBeast_UI.SchDoc | Drawn By: VM & IG

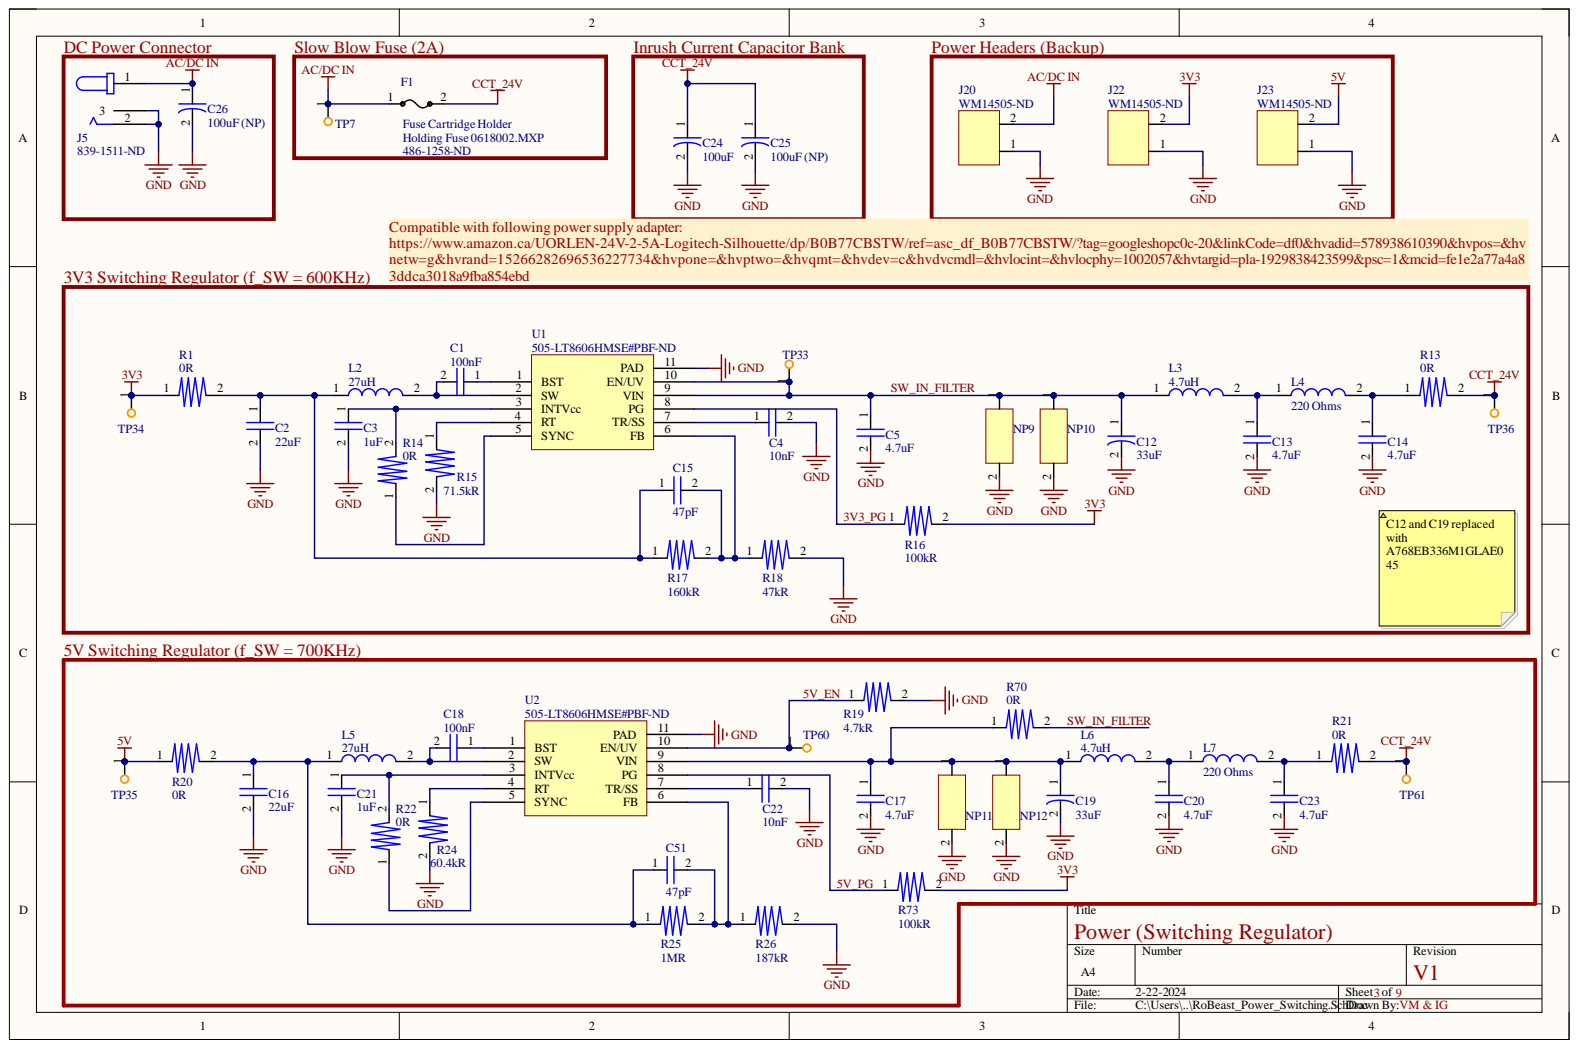
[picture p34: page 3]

Compatible with following powersupply adapter:
https://www.amazon.ca/UORLEN-24V-2-5A-Logitech-Silhouette/dp/B0B77CBSTW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
netw=g&hvrand=15266282696536227734&hvpone=&hvptwo=&hvqmt=&hvdev=c&hvdvcmdl=&hvlocint=&hvlocphy=1002057&hvtargid=pla-1929838423599&psc=1&mcid=fe1e2a77a4a8
3ddca3018a9fba854ebd

Title Power (Switching Regulator)

Size A4 | Number | Revision

Date: 2-22-2024 | Sheet of
File: C:\Users\..\RoBeast_Power_Switching.SchDr Doacwn By: | VM & IG

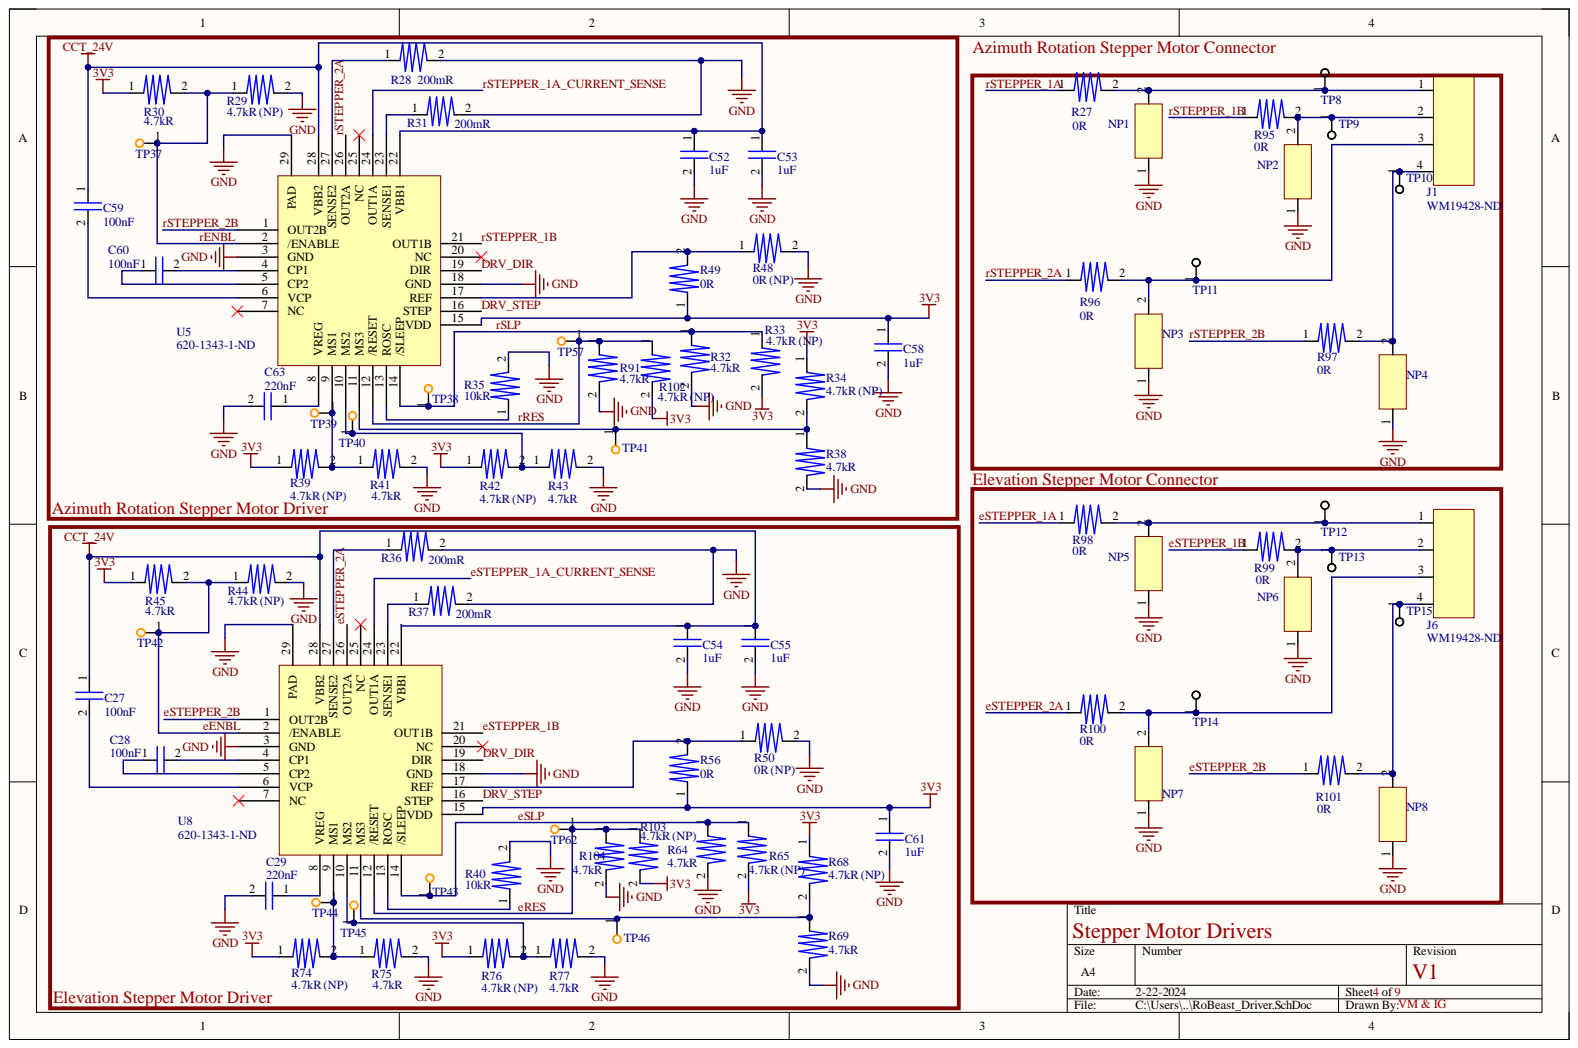
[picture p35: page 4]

Azimuth Rotation Stepper Motor Connector

r STEP PER_2 B | 1 | OUT 2 /ENAB GN D C P 1 C P 2 VC P N C

rEN B L | 2

Elevation Stepper Motor Connector

Azimuth Rotation Stepper Motor Driver

e STEP P ER_2 B | 1 | OUT 2 /ENAB GN D C P 1 C P 2 VC P N C

eEN B L | 2

Siz e A4 | Numb e r | R evisio n V1

Da te : 2-22-2 0 24 | She et of 4
File : C:\Use rs\. .\RoB e ast_Dr iv e r . S c hD o c | Dr awn By: I

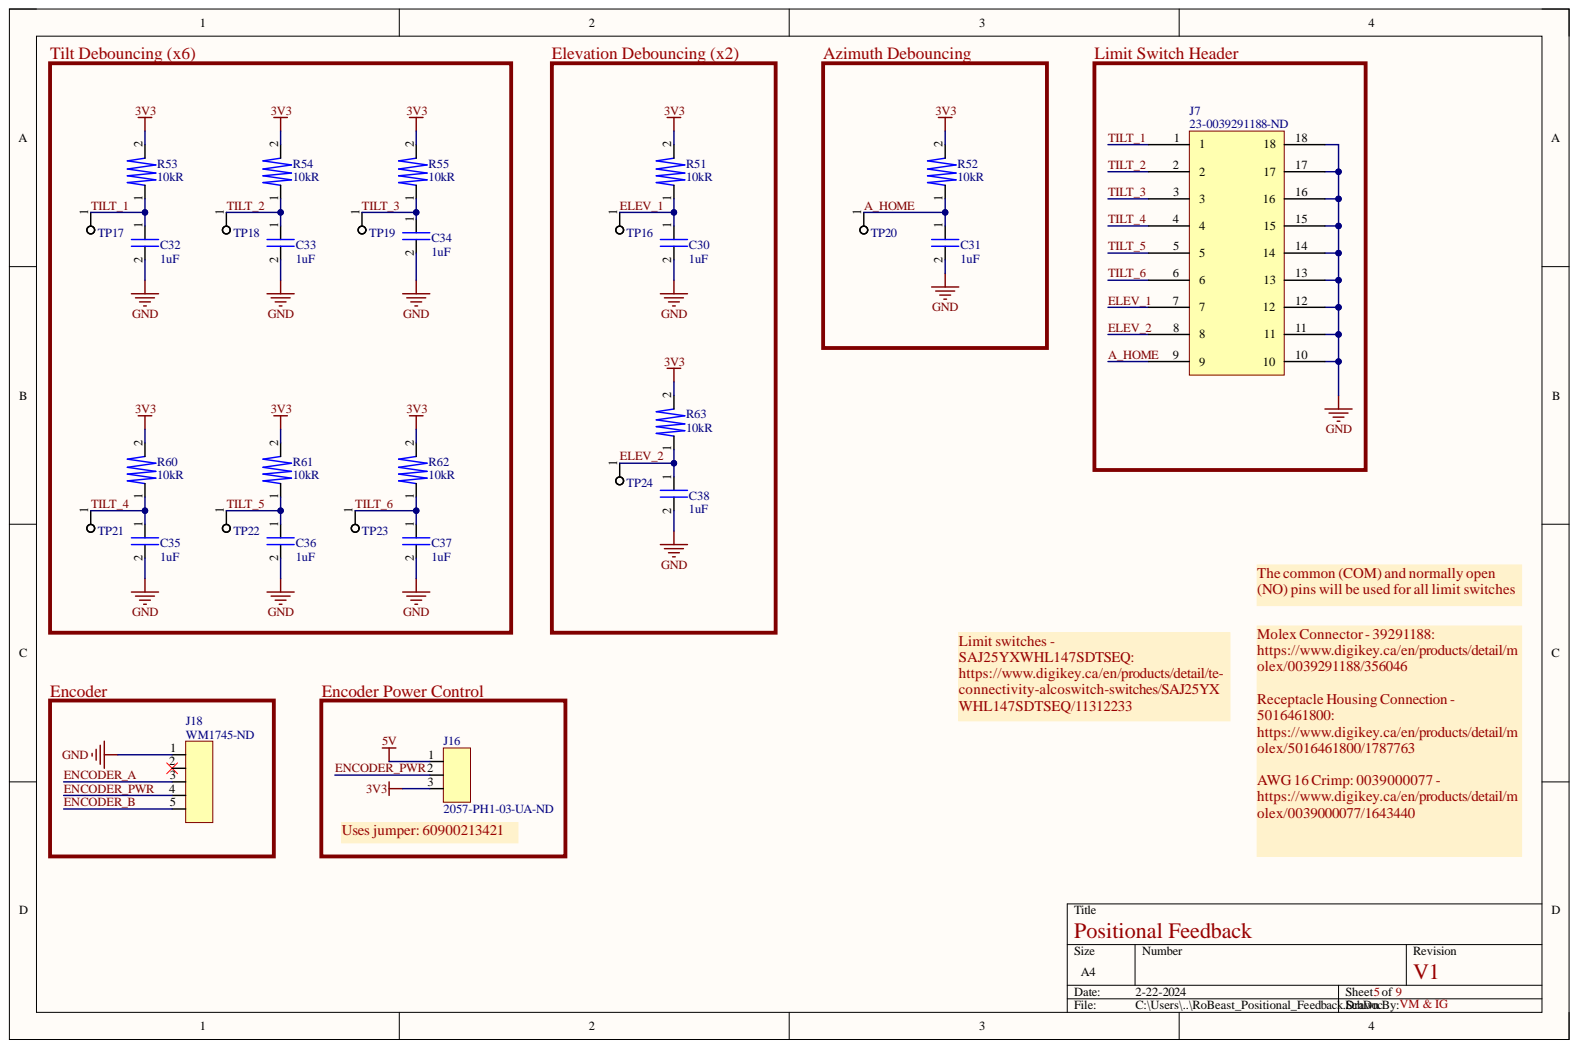
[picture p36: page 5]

Siz e A4 | Numb e r | R evisio n V1

Da te : 2-22-2 0 24 | She et of 5 9
File : C:\Use rs\. .\RoB e ast_Positional_F e e db a c | k .Dr SchaDwn ocBy: VM & I G

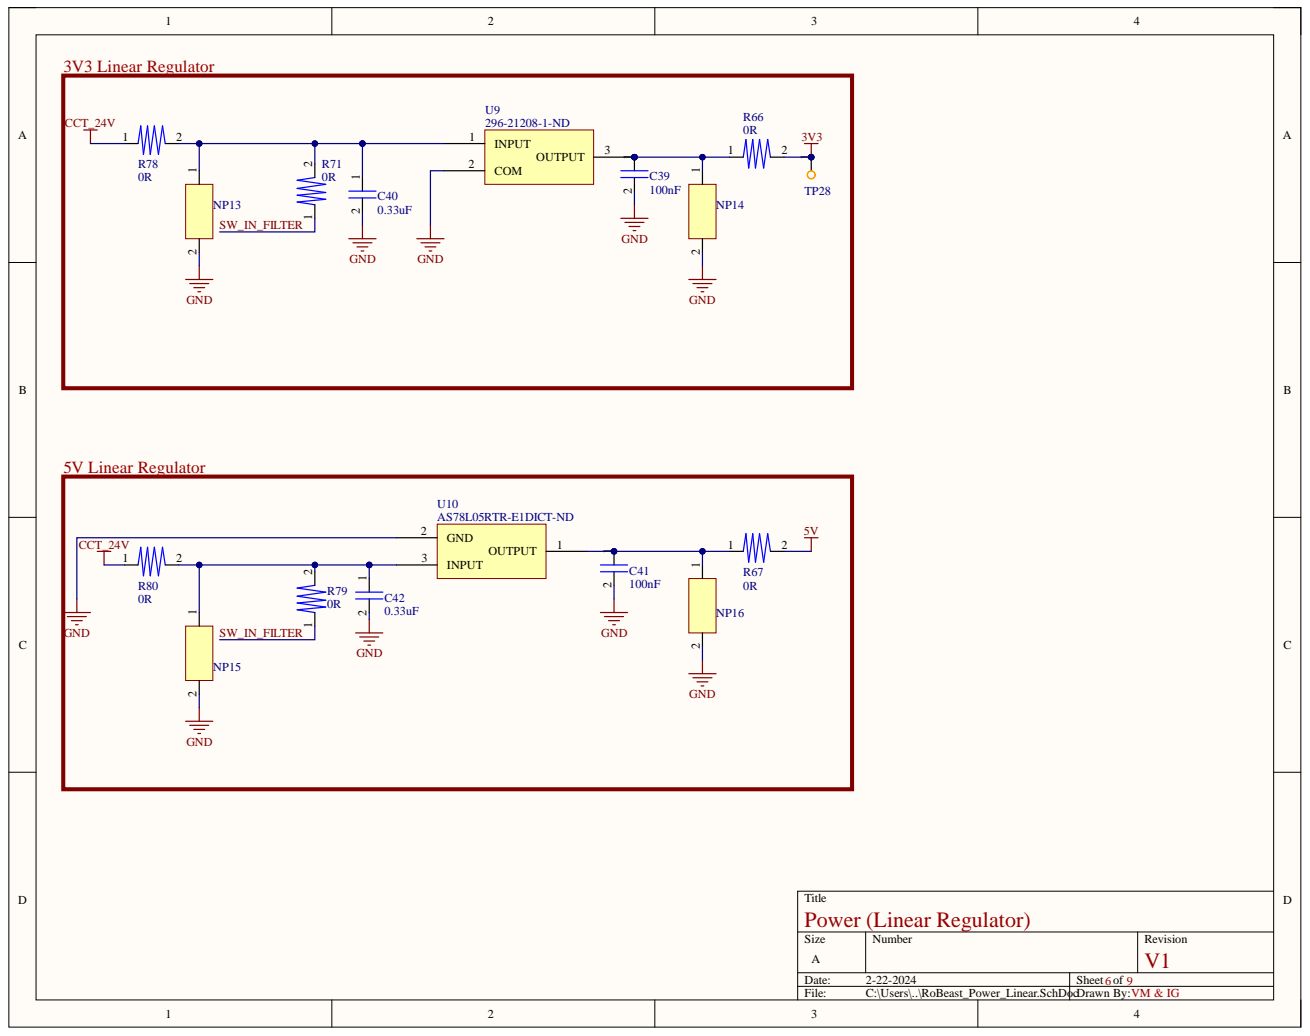
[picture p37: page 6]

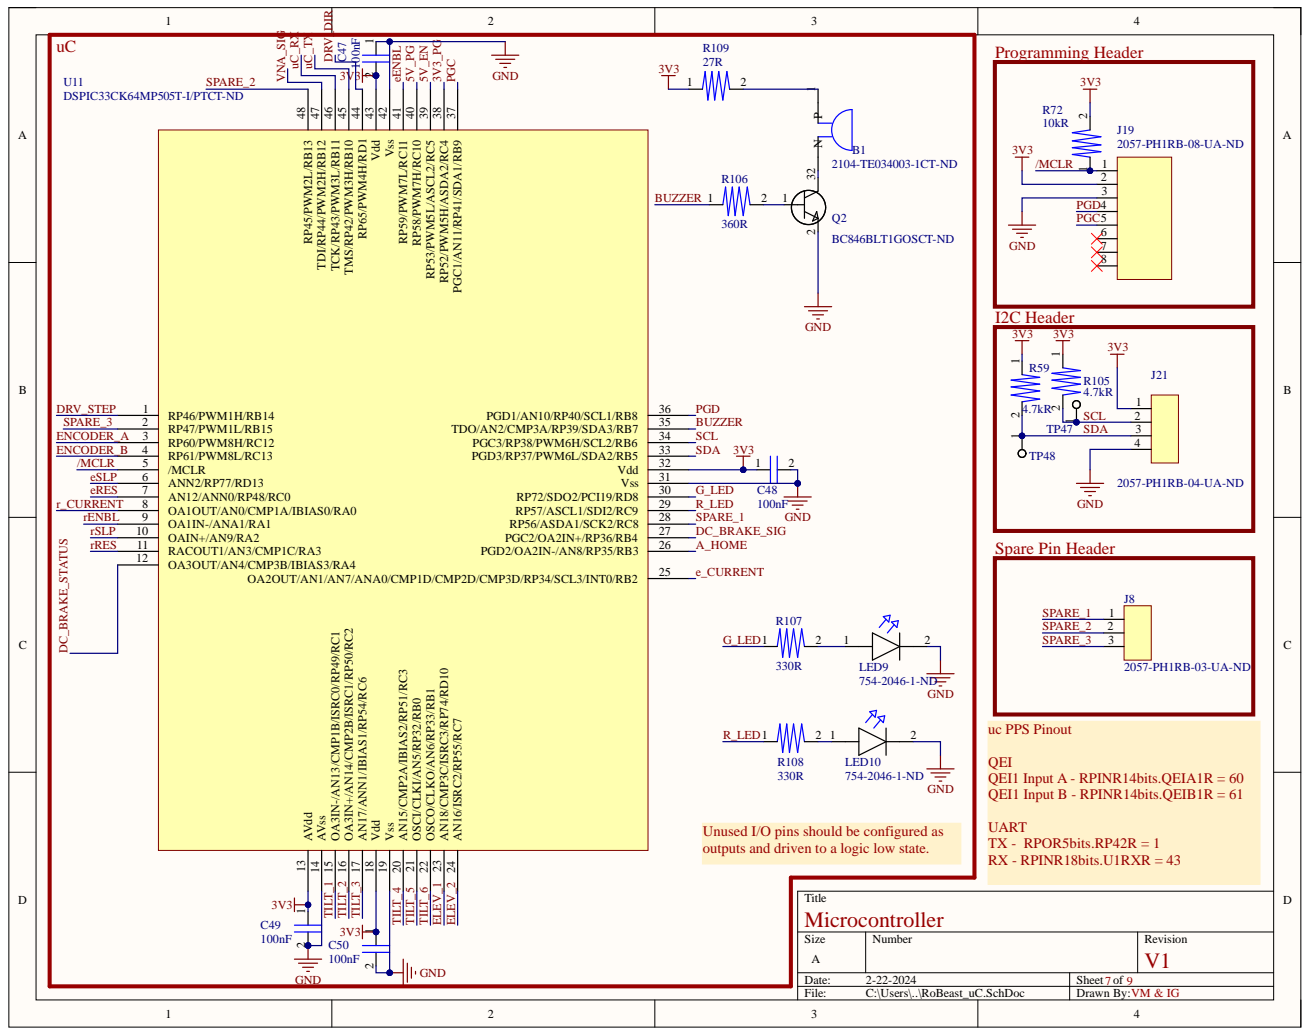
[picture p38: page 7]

TP47 | SCL

Unused I/O pins should be configured as
outputs and driven to a logic low state.

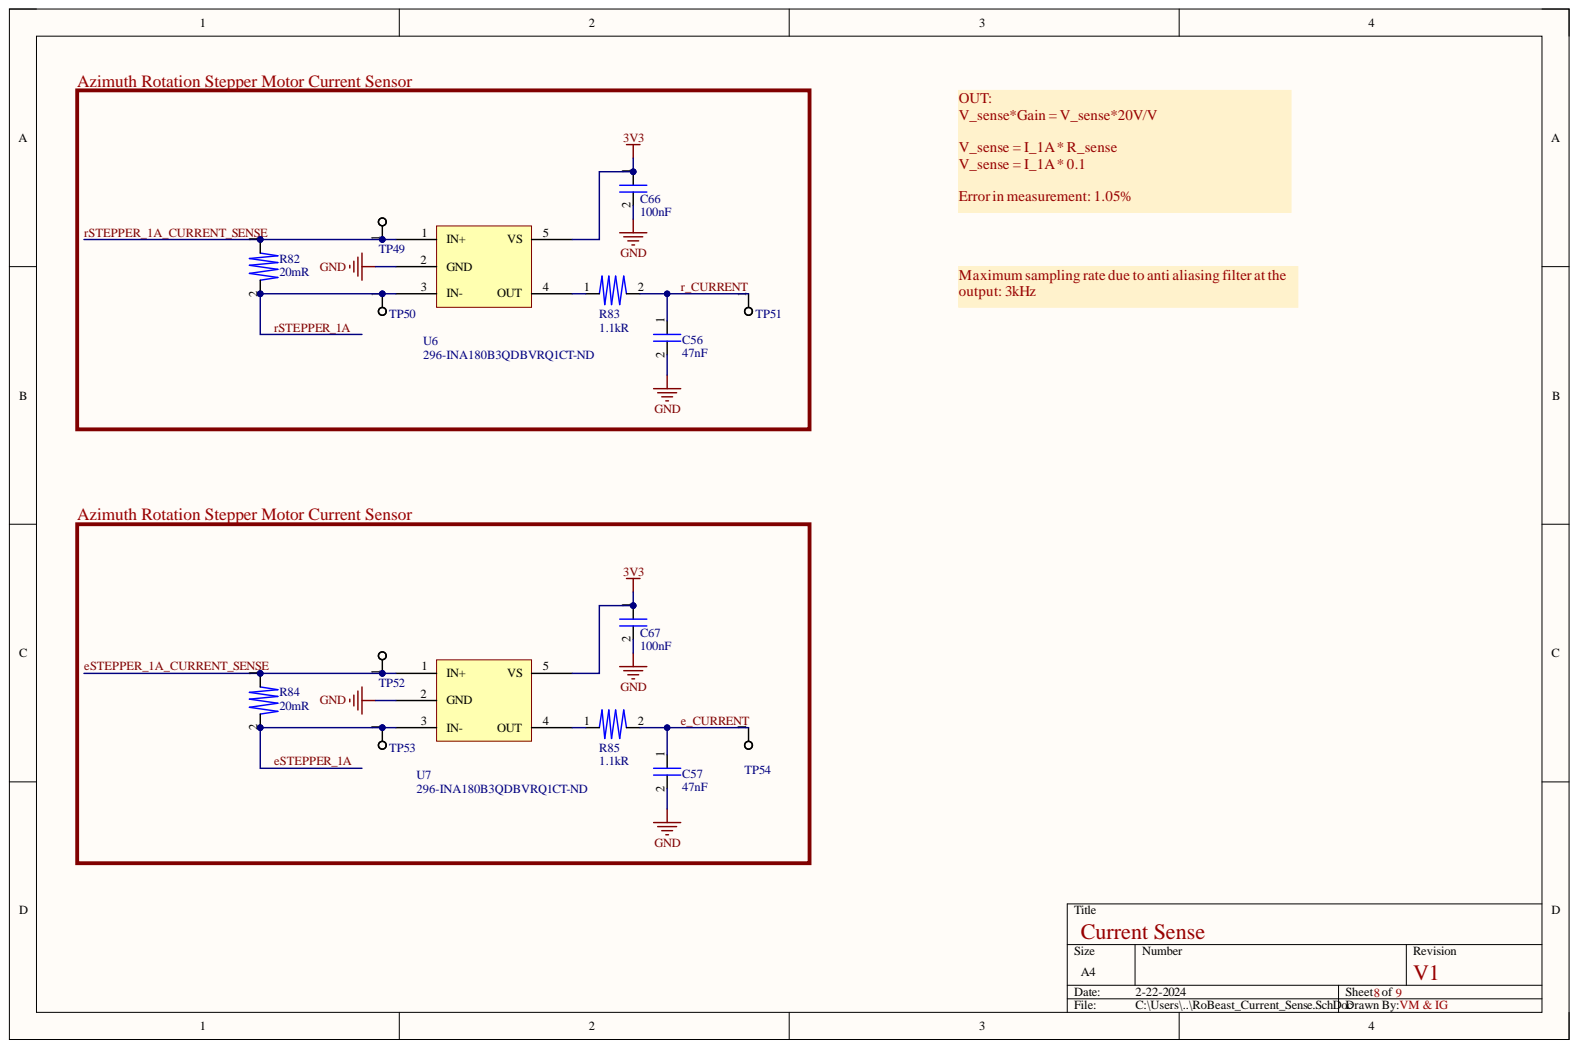
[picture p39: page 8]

Azimuth Rotation Stepper Motor Current Sensor

Maximum sampling rate due to anti aliasing filter at the

Size A4 | Number | Revision

Date: 2-22-2024 | Sheet of
File: C:\Users\..\RoBeast_Current_Sense.SchDoDr c awn By: | VM & IG

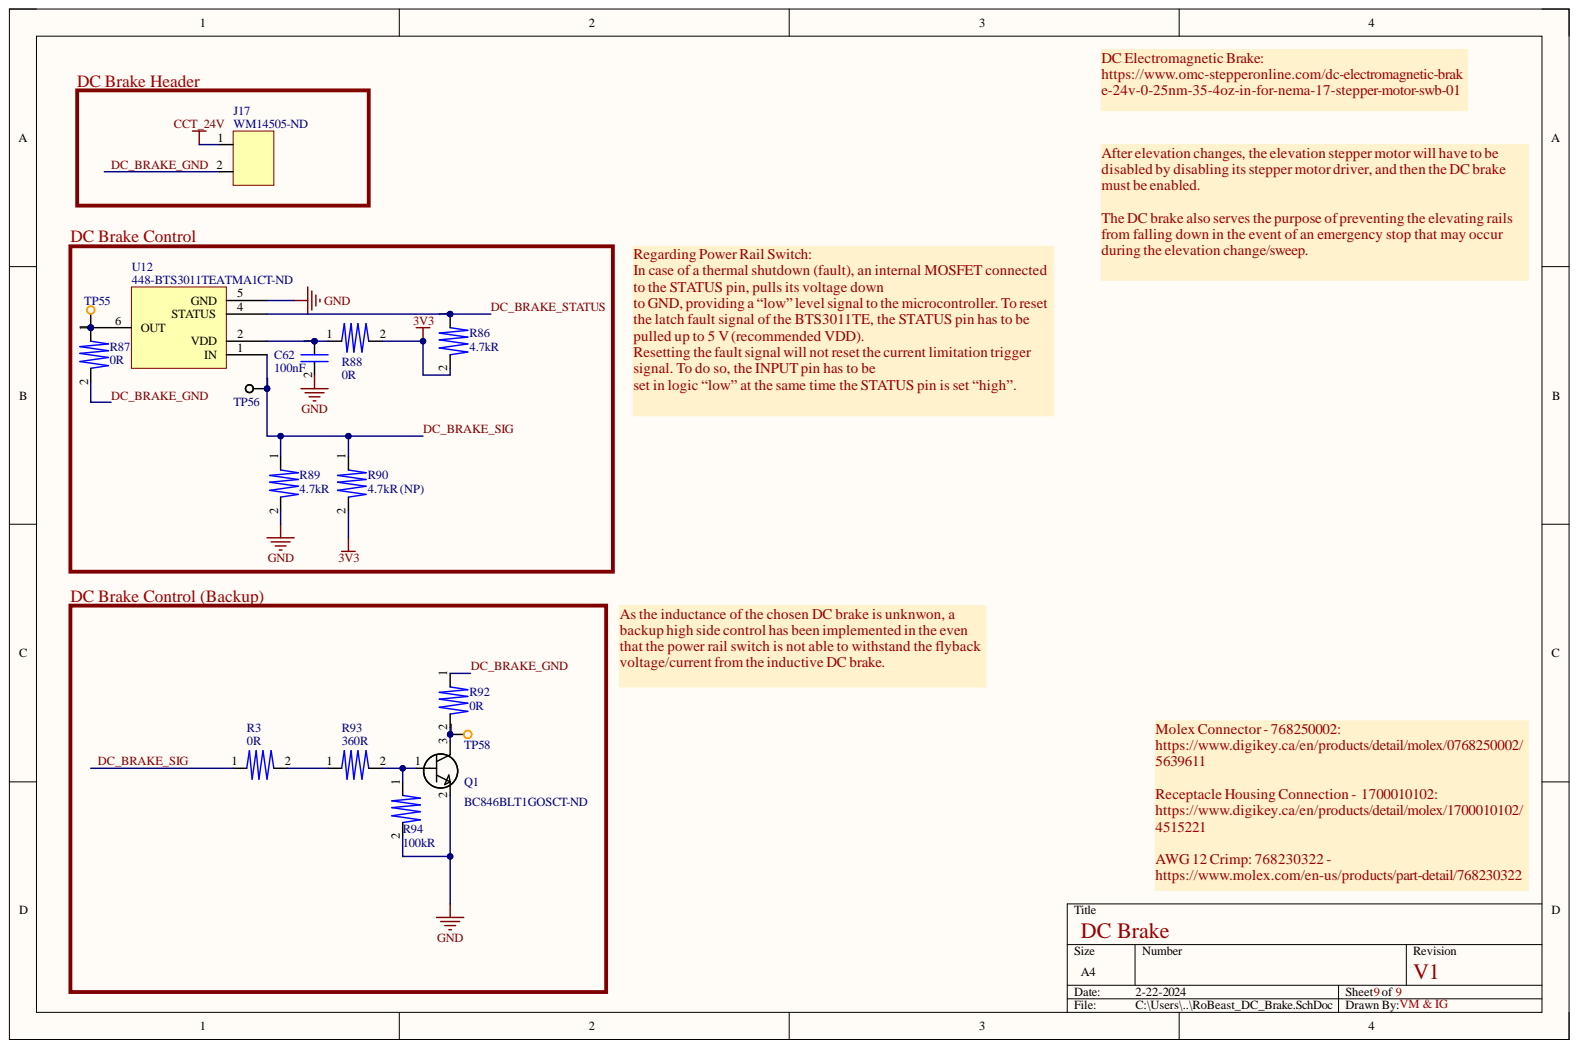
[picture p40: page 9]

DC Electromagnetic Brake:
https://www.omc-stepperonline.com/dc-electromagnetic-brak
e-24v-0-25nm-35-4oz-in-for-nema-17-stepper-motor-swb-01

disabled by disabling its stepper motor driver, and then the DC brake
must be enabled.

The DC brake also serves the purpose of preventing the elevating rails
from falling down in the event of an emergency stop that may occur
during the elevation change/sweep.

Regarding PowerRail Switch:
In case of a thermal shutdown (fault), an internal MOSFET connected
to the STATUS pin, pulls its voltage down
to GND, providing a “low” levelsignal to the microcontroller. To reset
the latch fault signal of the BTS3011TE, the STATUS pin has to be
pulled up to 5 V (recommended VDD).
Resetting the faultsignal will not reset the current limitation trigger
signal. To do so, the INPUT pin has to be
set in logic “low” at the same time the STATUS pin is set “high”.

DC Brake Control (Backup)

As the inductance of the chosen DC brake is unknwon, a
backup high side control has been implemented in the even
that the power rail switch is not able to withstand the flyback
voltage/current from the inductive DC brake.

Molex Connector- 768250002:
https://www.digikey.ca/en/products/detail/molex/0768250002/

Receptacle Housing Connection - 1700010102:
https://www.digikey.ca/en/products/detail/molex/1700010102/

AWG 12 Crimp: 768230322 -
https://www.molex.com/en-us/products/part-detail/768230322

Size A4 | Number | Revision

Date: 2-22-2024 | Sheet of
File: C:\Users\..\RoBeast_DC_Brake.SchDoc | Drawn By: VM & IG

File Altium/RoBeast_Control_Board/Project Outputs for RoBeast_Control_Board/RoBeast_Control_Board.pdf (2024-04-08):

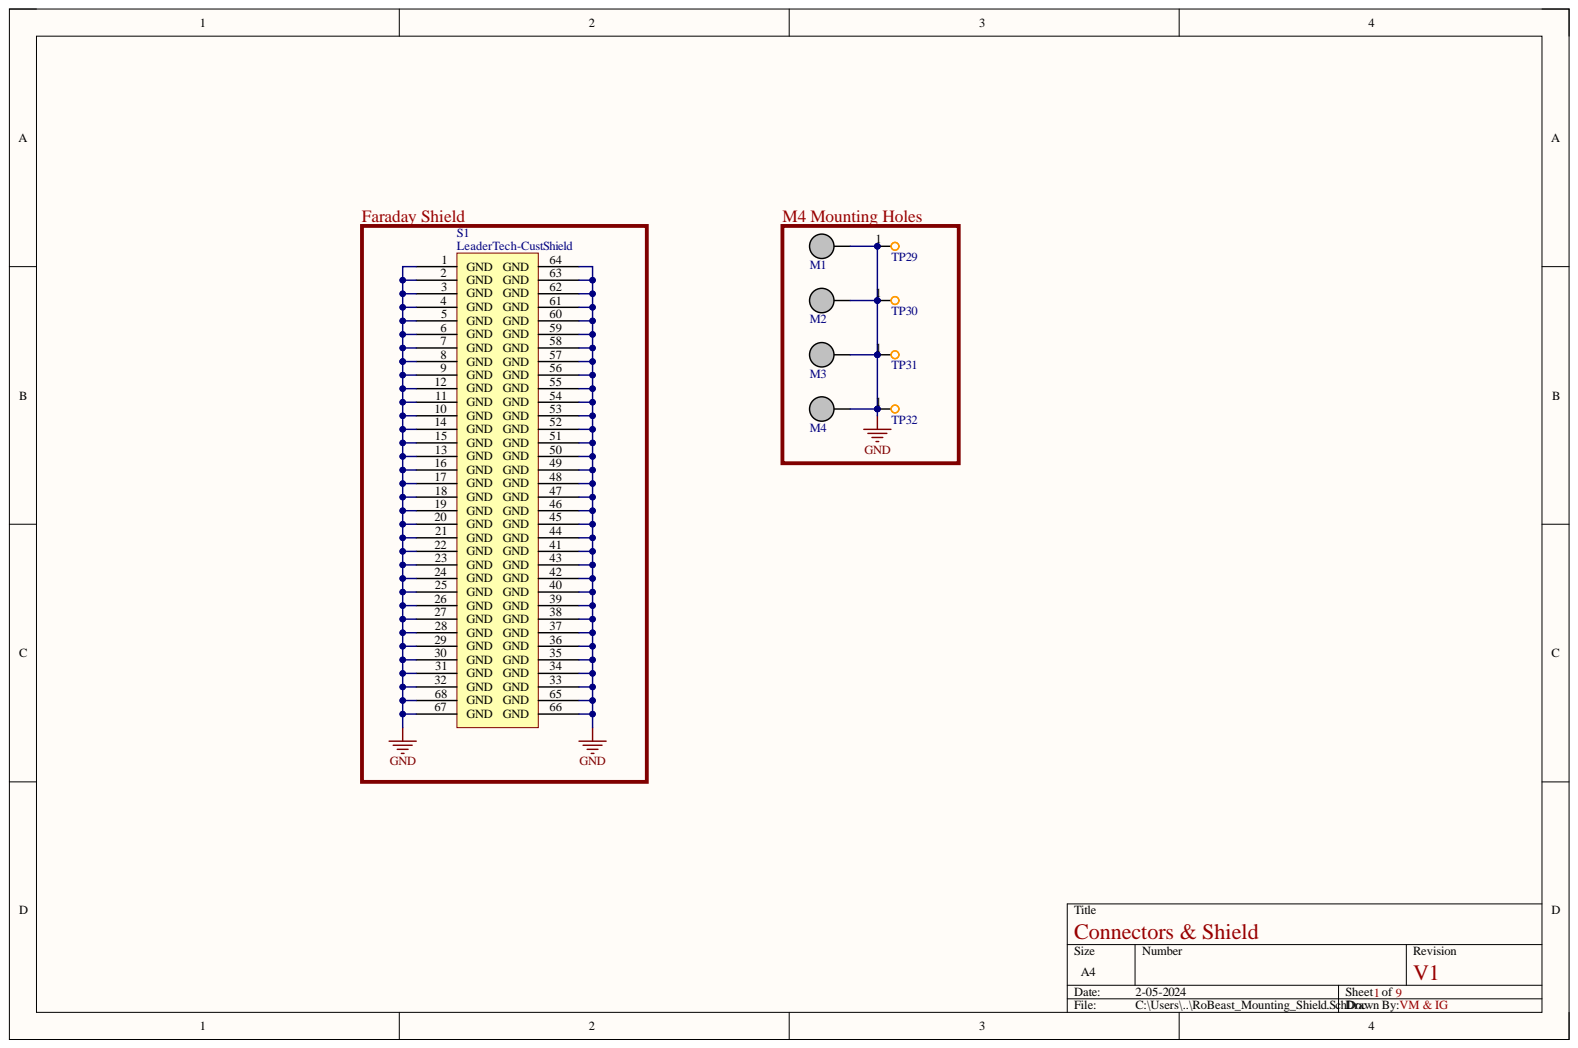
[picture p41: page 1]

Siz e A4 | Numb e r | R evisio n V1

Da te : 2-05-2 0 24 | She et of 1 9
File : C:\Use rs\. .\RoB e ast_Mounting_Shie l d . S | c hDr Doacwn By: VM & I G

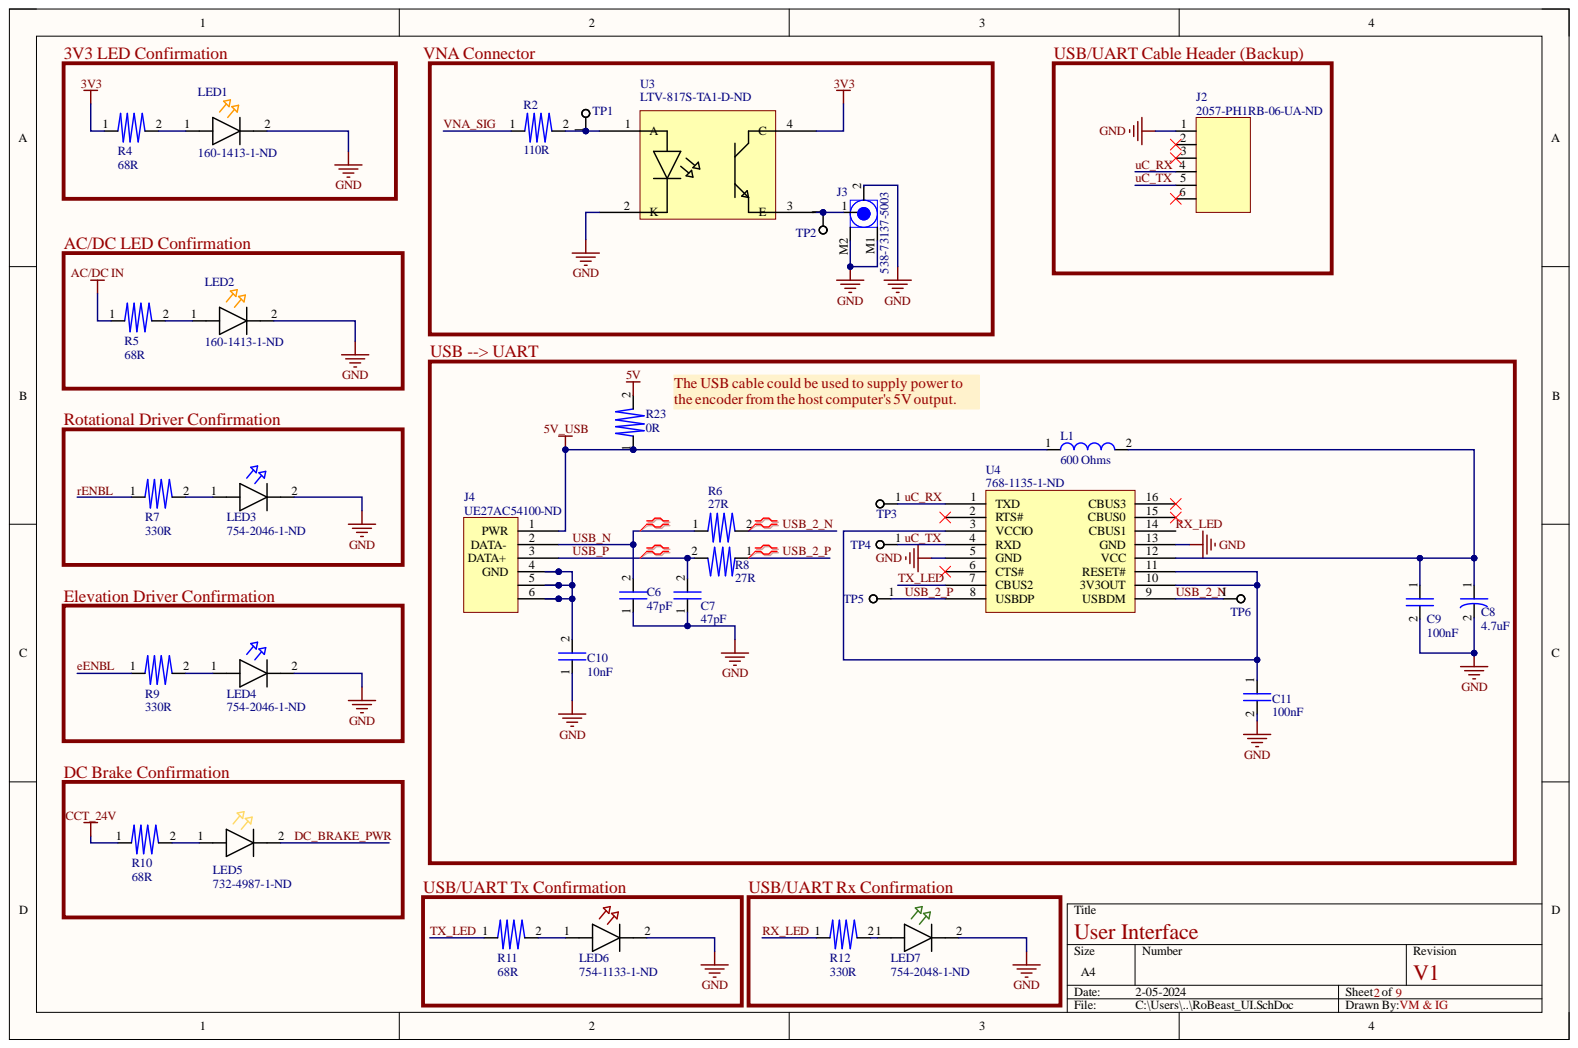
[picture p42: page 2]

USB/UART Cable Header (Backup)

AC/DC LED Confirmation

the encoderfrom the host computer's 5Voutput.

Size A4 | Number | Revision

Date: 2-05-2024 | Sheet of
File: C:\Users\..\RoBeast_UI.SchDoc | Drawn By: VM & IG

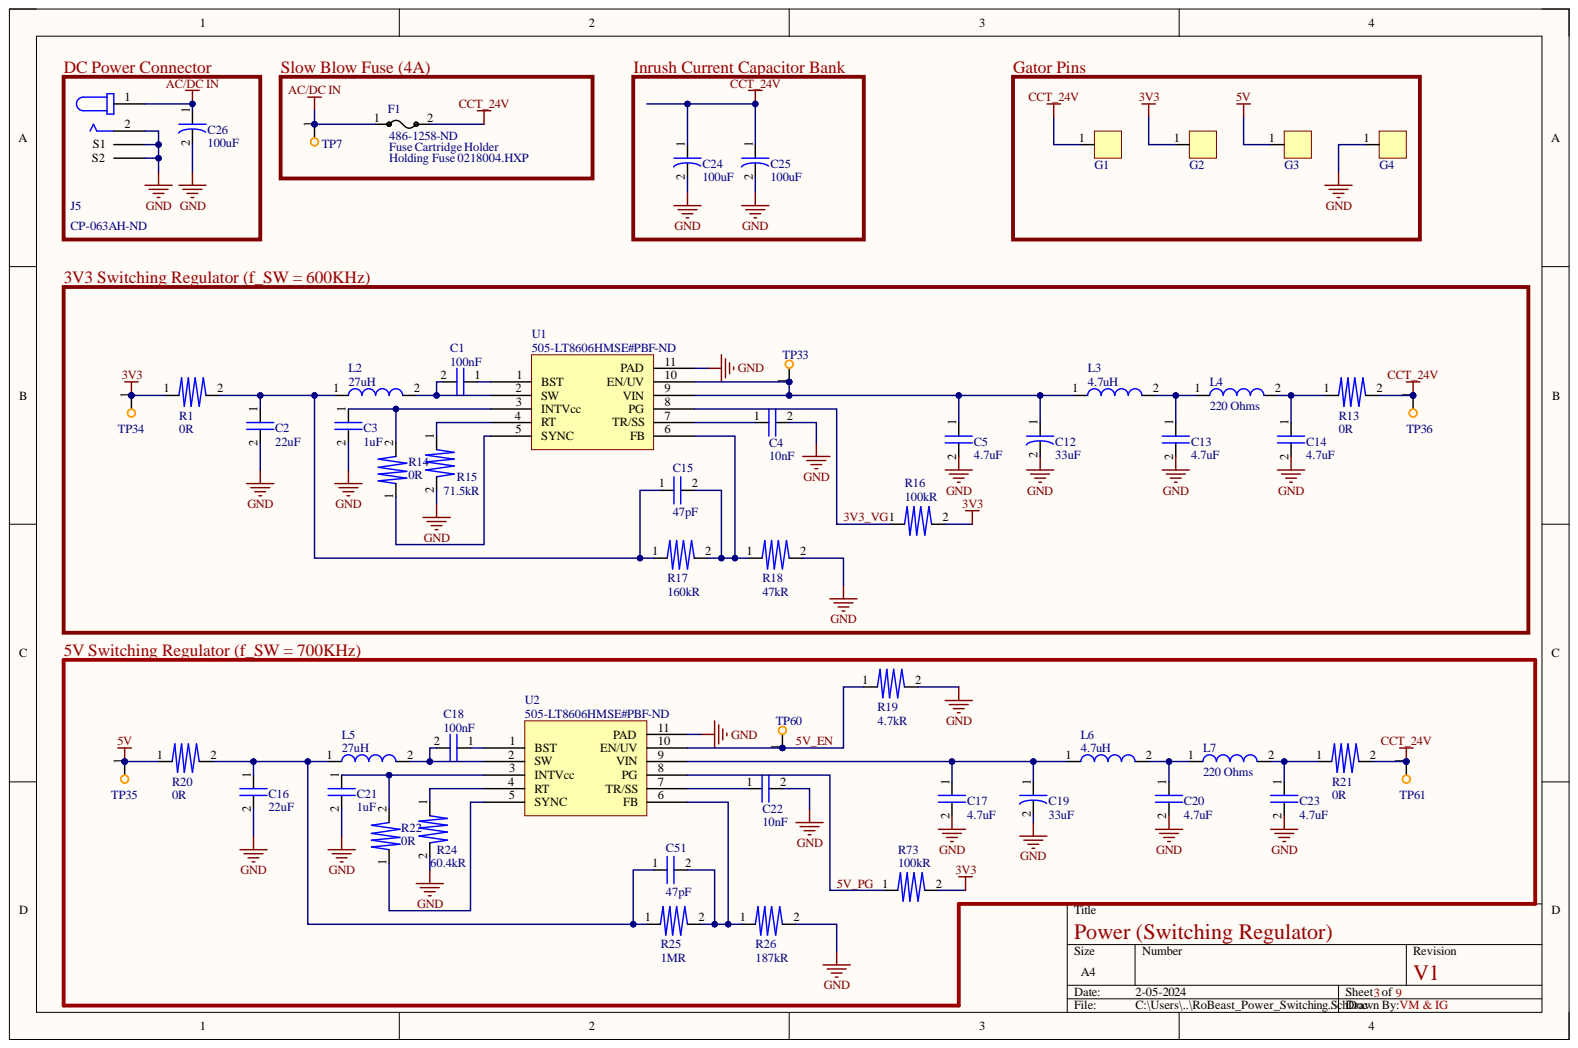
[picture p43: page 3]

Inrush Current Capacitor Bank

Title Power (Switching Regulator)

Size A4 | Number | Revision

Date: 2-05-2024 | Sheet of
File: C:\Users\..\RoBeast_Power_Switching.SchDr Doacwn By: | VM & IG


4 V | Azimuth Rotation Stepper Motor Connector

rEN B L | 2

Elevation Stepper Motor Connector

Azimuth Rotation Stepper Motor Driver

e STEP P ER_2 B | 1 | OUT 2 /ENAB GN D C P 1 C P 2 VC P N C

eEN B L | 2


Azimuth Rotation Home Switch

The common (COM) and normally open
(NO) pins will be used for all limit switches

Molex Connector- 26013114:
https://www.mouser.ca/ProductDetail/Molex
/26-01-3114?qs=ZhwKFWhxrSEC8%252B
v2mQsO9A%3D%3D

Receptacle Housing Connection -
https://www.digikey.com/en/products/detail/
molex/0039013025/3160115

Pre-crimped AWG 18 Wire: 797580009 -
molex/0797580009/5806729

Size A4 | Number | Revision

Date: 2-05-2024 | Sheet of
File: C:\Users\..\RoBeast_Positional_Feedback.Dr SchaDwn ocBy: | VM & IG




Azimuth Rotation Stepper Motor Current Sensor

Maximum sampling rate due to anti aliasing filter at the
output: 3kHz

Size A4 | Number | Revision

Date: 2-05-2024 | Sheet of
File: C:\Users\..\RoBeast_Current_Sense.SchDoDr c awn By: | VM & IG


DC Electromagnetic Brake:
https://www.omc-stepperonline.com/dc-electromagnetic-brak

e-24v-0-25nm-35-4oz-in-for-nema-17-stepper-motor-swb-01 DC Brake Header (Bigger AWG Backup)

disabled by disabling its stepper motor driver, and then the DC brake
must be enabled.

The DC brake also serves the purpose of preventing the elevating rails
from falling down in the event of an emergency stop that may occur
during the elevation change/sweep.

Regarding PowerRail Switch:
In case of a thermal shutdown (fault), an internal MOSFET connected to
the STATUS pin, pulls its voltage down
to GND, providing a “low” levelsignal to the microcontroller. To reset
the latch fault signal of the BTS3011TE, the STATUS pin has to be
pulled up to 5 V (recommended VDD).
Resetting the faultsignal will not reset the current limitation trigger
signal. To do so, the INPUT pin has to be
set in logic “low” at the same time the STATUS pin is set “high”. I

DC Brake Control (Backup)

As the inductance of the chosen DC brake is unknwon, a
backup high side control has been implemented in the even
that the power rail switch is not able to withstand the flyback
voltage/current from the inductive DC brake.

Molex Connector- 26013114:
https://www.mouser.ca/ProductDetail/Molex/26-01-3114?q
s=ZhwKFWhxrSEC8%252Bv2mQsO9A%3D%3D

Receptacle Housing Connection - 39013025:
https://www.digikey.com/en/products/detail/molex/003901

Pre-crimped AWG 18 Wire: 797580009 -
https://www.digikey.com/en/products/detail/molex/079758

Size A4 | Number | Revision

Date: 2-05-2024 | Sheet of
File: C:\Users\..\RoBeast_DC_Brake.SchDoc | Drawn By: VM & IG

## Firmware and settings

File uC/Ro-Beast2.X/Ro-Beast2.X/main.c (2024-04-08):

/*
 * File:   main.c
 * Author: Ro-Beast Battle Busters
 */

#include "system.h"
#include "state_select.h"
#include "global_variables.h"
#include "timer.h"
#include "tmr1.h"
#include "driver.h"
#include "pwm.h"

int main(void)
{
    SYSTEM_Initialize();
    driver_Start();
    TMR1_Start();
    elev_1 = PORTDbits.RD10;
    elev_2 = PORTCbits.RC7;
    azimuth_home = PORTBbits.RB3;
    VNA_Enable();
    robeast_state = robeast_init;
    State_Select();
    return 1; 
}

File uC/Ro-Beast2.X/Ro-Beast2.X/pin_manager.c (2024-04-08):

/*
 * File:   pin_manager.c
 * Author: Ro-Beast Battle Busters (with assistance from the MCC)
 */

#include <xc.h>
#include <stdio.h>
#include "pin_manager.h"

void PIN_MANAGER_Initialize (void)
{
    /****************************************************************************
     * Setting the Output Latch SFR(s)
     ***************************************************************************/
    LATA = 0x0000;
    LATB = 0x0000;
    LATC = 0x0000;
    LATD = 0x0000;

    /****************************************************************************
     * Setting the GPIO Direction SFR(s)
     ***************************************************************************/
    TRISA = 0x0011;
    TRISB = 0x0B6D;
    TRISC = 0x37DE;
    TRISD = 0x0400;

    /****************************************************************************
     * Setting the Weak Pull Up and Weak Pull Down SFR(s)
     ***************************************************************************/
    CNPDA = 0x0000;
    CNPDB = 0x0000;
    CNPDC = 0x0000;
    CNPDD = 0x0000;
    CNPUA = 0x0000;
    CNPUB = 0x0000;
    CNPUC = 0x0000;
    CNPUD = 0x0000;

    /****************************************************************************
     * Setting the Open Drain SFR(s)
     ***************************************************************************/
    ODCA = 0x0000;
    ODCB = 0x0000;
    ODCC = 0x0000;
    ODCD = 0x0000;

    /****************************************************************************
     * Setting the Analog/Digital Configuration SFR(s)
     ***************************************************************************/
    ANSELA = 0x0000;
    ANSELB = 0x0000;
    ANSELC = 0x0000;
    ANSELD = 0x0000;
    
    /****************************************************************************
     * Set the PPS
     ***************************************************************************/
    __builtin_write_RPCON(0x0000); // unlock PPS

    RPINR18bits.U1RXR = 0x002B;    //RB11->UART1:U1RX
    RPOR5bits.RP42R = 0x0001;    //RB10->UART1:U1TX

    RPINR3bits.ICM1R = 47;          //remapping input pin set by the PWM-Initialize function as a SCCP pin for counting
    
    //using PPS to set pin 60 and 61 to QEIA and QEI respectively
    RPINR14bits.QEIA1R = 60;
    RPINR14bits.QEIB1R = 61;

    
    RPINR0bits.INT1R = 35; // a_home (RB3)
    RPINR1bits.INT2R = 74; // elev_1 (bottom) (RD10)
    RPINR1bits.INT3R = 55; // elev_2 (top) (RC7)

            
    __builtin_write_RPCON(0x0800); // lock PPS
}

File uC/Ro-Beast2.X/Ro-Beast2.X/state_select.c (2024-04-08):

/*
 * File:   state_select.c
 * Author: Ro-Beast Battle Busters
 */

#include "xc.h"
#include "state_select.h"
#include "global_variables.h"
#include "driver.h"
#include "pwm.h"
#include "stdlib.h"
#include "stddef.h"
#include "qei.h"
#include "tmr1.h"
#include "uart.h"


#define FCY 4000000UL       //FRC/2
#include "libpic30.h"


void State_Select(void)
{
    while(1){
        switch(robeast_state)
        {   
            case robeast_init:
                
                uart_index = 0;
                rx_msg = 0x00; 

                if (elev_1 != 0) {      //elev_1 = bottom limit switch, elev_2 = top limit switch
                    PWM1_Reset(5,'e');
                    driverE_Enable('d');  
                } else {
                    current_height = 104.0;
                }
                
                while (current_height != 104.0) {}

                if (azimuth_home != 0) {
                    PWM1_Reset(30, 'a');
                    driverA_Enable('l');    
                }else {
                    current_azimuth = 0;
                }

                while (current_azimuth != 0) {}

                robeast_state = robeast_standby;

                break;

            case robeast_position:
                
                IEC0bits.INT1IE = 0;
                LATDbits.LATD8 = 0;
                uart_index = 0;
                rx_msg = 0x00;   
                
                current_height = 104.0;
                desired_height = atof(desired_height_char);
                
                current_azimuth = 0;
                desired_azimuth = atof(desired_azimuth_char);
                
                //current_height = atof(curr_height_char);
                               
                VNA_EMeasurementTriggerCalculation(2);
                
                SCCP_EStopCriteria(desired_height, current_height);
                SCCP_Enable();

                if ((int)current_height != (int)desired_height) {
                    PWM1_Reset(10,'e');
                    driverE_Enable('u');    
                }

                while ((int) current_height != (int) desired_height) {}
                VNA_Reset();
                
                

                VNA_AMeasurementTriggerCalculation(5);
                
                if ((int) current_azimuth != (int) desired_azimuth) {
                    PWM1_Reset(30, 'a');
                    driverA_Enable('l');    
                    QEI_Initialize();                               //have to initialize every time direction is changed due to the register values changing for compare registers
                    QEI_CounterClear();
                    QEI_CounterSet(desired_azimuth);
                }
                
                while(current_azimuth != desired_azimuth) {}         
                
                current_azimuth = 0;
                VNA_Reset();                                    //resets VNA signal back to a HIGH

                IEC0bits.INT1IE = 1;
                robeast_state = robeast_standby;
                //robeast_state = robeast_azimuth_sweep;
                
                break;

            case robeast_height_sweep:
                uart_index = 0;
                rx_msg = 0x00; 
                
                desired_height = atof(desired_height_char);
                current_height = atof(curr_height_char); 
                
                desired_height_interval = atof(desired_height_interval_char);
                //desired_height_interval = desired_height_interval*1000;
                desired_height_speed = atof(desired_height_speed_char);
                               
                VNA_EMeasurementTriggerCalculation(desired_height_interval);
                
                SCCP_EStopCriteria(desired_height, current_height);
                SCCP_Enable();

                PWM1_Reset(desired_height_speed,'e');
                driverE_Enable('u');

                while ((int) current_height != (int) desired_height) {}
                VNA_Reset();
                
                robeast_state = robeast_init;
                
                break;

            case robeast_azimuth_sweep:
                uart_index = 0;
                rx_msg = 0x00; 
                
                IEC0bits.INT1IE = 0;
                
                desired_azimuth = atof(desired_azimuth_char);
                current_azimuth = 0; 
                
                desired_azimuth_interval = atof(desired_azimuth_interval_char);
                desired_azimuth_speed = atof(desired_azimuth_speed_char);

                VNA_AMeasurementTriggerCalculation(desired_azimuth_interval);
                
                //VNA_AMeasurementTriggerCalculation(2);
                
                PWM1_Reset(desired_azimuth_speed, 'a');
                //PWM1_Reset(25, 'a');
                driverA_Enable('l');    
                
                QEI_Initialize();                               //have to initialize every time direction is changed due to the register values changing for compare registers
                QEI_CounterClear();
                QEI_CounterSet(desired_azimuth);
                while(current_azimuth != desired_azimuth) {
                    if (POS1CNTL % vna_measurement_trigger == 0){
                        vna_measurement_trigger_off = (int) (POS1CNTL + (vna_measurement_trigger/2));
                        LATBbits.LATB12 = 0; //only want a small falling edge trigger
                        LATDbits.LATD8 = 1;
                    }
                    if (vna_measurement_trigger_off == POS1CNTL){
                        LATBbits.LATB12 = 1; //set VNA signal as HIGH again
                        LATDbits.LATD8 = 0;
                    }   
                }                
                current_azimuth = 0;
                desired_azimuth = atof(desired_azimuth_char);
                VNA_Reset();                                    //resets VNA signal back to a HIGH

                
                PWM1_Reset(30, 'a');
                driverA_Enable('r');                            //moving opposite direction to untangle cables after sweep is complete
                
                QEI_Initialize();                               
                QEI_CounterClear();
                QEI_CounterSet(desired_azimuth);
                while( current_azimuth != desired_azimuth) {}                
                current_azimuth = 0;
                VNA_Reset();                                    //resets VNA signal back to a HIGH

                IEC0bits.INT1IE = 1;
                
                robeast_state = robeast_init;
                
                break;

            case robeast_pause:

            case robeast_cancel:

            case robeast_fault:
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

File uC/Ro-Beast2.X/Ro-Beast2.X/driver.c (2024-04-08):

/*
 * File:   driver.c
 * Author: Ro-Beast Battle Busters
 */

#include "xc.h"
#include "pwm.h"
#include "stdio.h"

void driverE_Enable(char dir){
    if (dir == 'u') {
        LATDbits.LATD1 = 0;
    } else if (dir == 'd') {
        LATDbits.LATD1 = 1;
    }
    // DC Brake
    LATBbits.LATB4 = 1;
    // eENABLE
    LATCbits.LATC11 = 0;
    // eSLEEP
    LATDbits.LATD13 = 1;
    // eRES
    LATCbits.LATC0 = 1;
    PWM_Enable();
}

void driverA_Enable(char dir){
    // l = ccw, r = cw (looking down on table)
    if (dir == 'l') {
        LATDbits.LATD1 = 0;
    } else if (dir == 'r') {
        LATDbits.LATD1 = 1;
    }

    // rENABLE
    LATAbits.LATA1 = 0;
    // rSLEEP
    LATAbits.LATA2 = 1;
    // rRES
    LATAbits.LATA3 = 1;
    PWM_Enable();
}

void driverE_Disable(void){
    // eENABLE
    LATCbits.LATC11 = 1;
    // eSLEEP
    LATDbits.LATD13 = 0;
    // eRES
    LATCbits.LATC0 = 0; 
    // DC Brake
    LATBbits.LATB4 = 0;
    PWM_Disable();
}

void driverA_Disable(void){
    // rENABLE
    LATAbits.LATA1 = 1;
    // rSLEEP
    LATAbits.LATA2 = 0;
    // rRES
    LATAbits.LATA3 = 0;

    PWM_Disable();
}

void driver_Start(void){
    driverE_Disable();
    driverA_Disable();
}
